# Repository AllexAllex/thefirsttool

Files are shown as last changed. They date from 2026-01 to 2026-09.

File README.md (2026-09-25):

# Информация о станках The First Tool (thefirsttool, firsttool, tool the first)

## Оглавление:
1. [Доработки](#раздел_доработки)
2. [Настройка станка](#раздел_настройка)
3. [3D модели для печати](#раздел_модели)
4. [Информация](#раздел_информация)
5. [Ссылки](#раздел_ссылки)
6. [Прочие дела станочные](#прочее)
   
## 1. Доработки 
- [Первая доработка - замена винтов](modification/screw-m3/screw-m3.md)
- [Фрезерный стол из станочного профиля](/modification/milling-table/milling-table.md)
- [Доработка тисков](modification/vise/vise.md)
- [Перевод на трапецидальную винт-гайку Т5 кареток станка](modification/screw-t5/screw-t5.md)
- [Замена втулок М6 на резьбовые втулки М6-М8](https://youtu.be/2hZVbYo9hZk)
- [Вращающиеся лимбы](modification/limb/limb.md)
- [Распиливание разжимных клинов](modification/sawing-wedge/sawing-wedge.md)
- [Оклеивание направляющих стальной лентой](modification/steel-tape/steel-tape.md)
- [Латунный клин в каретку](modification/brass-wedge/brass-wedge.md)
- [Выравнивание поверхности ласточкиного хвоста малой каретки](modification/low-feed-grinding/low-feed-grinding.md)
- [Исправление геометрии малой (поперечной) каретки](modification/small-feed-geometry/small-feed-geometry.md)
- [Прижимные винты клина подачи](modification/pressure-feed-screws/pressure-feed-screws.md)
- [Защита от стружки на шпиндель](modification/chip-protection/chip-protection.md)
- [Крепление фрезерной колонны (из двух длинных балок)](modification/milling-machine-column/milling-machine-column.md)
- [Крепление фрезерной колонны (из двух длинных балок) версия 2](modification/milling-machine-column-2/milling-machine-column-2.md)
- [Цанговый патрон ER20 на стандартный шпиндель](modification/er20/er20.md)
- [Проставка 25мм под моторный блок](modification/spacer-for-spindle/spacer-for-spindle.md)
- [Внедрение стального патрона и шпинделя с резьбой М14х1](modification/steel-lathe-chuck/steel-lathe-chuck.md)

## 2. Настройка станка 
- [Варианты сборки станков](/settings/assembly.md)
- [Регулировка плавности хода подачи](/settings/feed-flow.md)
- [Сборка и настройка фрезерного варианта станка](/settings/milling-machine.md)
- [Затяжка распорных клиньев](/settings/tightening-wedges.md)
  
## 3. 3D модели для печати 
- [Крышка моторного блока](/3d/engine-block-cover/engine-block-cover.md)
- [Защитный кожух на голову моторного блока для горизонтального фрезера](/3d/motor-protection-horizontal-milling/motor-protection-horizontal-milling.md)
- [Держатель ручки сверлильного станка](/3d/drilling-machine-lever-holder/drilling-machine-lever-holder.md)
- [Кондуктор для фрезеровки гаек Т5](3d/conductor-nuts-t5/conductor-nuts-t5.md)

## 4. Информация 
- [Ответы на часто задаваемые вопросы](/info/faq.md)
- [Сравнение станков The first tool с аналогами (Xendoll и тд)](/info/compare.md)
- [Чертежи частей станка](/info/drawings.md)
- [Каталог со всеми вариантами станков](/info/catalog.md)
- [Каталог частей станков](/info/catalog-parts.md)
- [Документы к станку: гарантийный талон, инструкция, сертификат](/info/passport.md)

## 5. Ссылки 
- [Наш канал в telegram](https://t.me/MiniLatheRussia)
- [Чат в telegram по модульным станкам The fist tools \ Xendoll \ Unimat и другим](https://t.me/TheFirstToolRussia)
- [Канал Игорь KLIV, много полезных доработок и примеров работ на станке](https://www.youtube.com/channel/UCZDuRbTqA5QuboGSG2y2jEQ)
- [Канал Эрик Плотник, много полезных доработок и примеров работ на станке](https://www.youtube.com/user/1149G)
- [Тема по станку на форуме судомоделистов](https://www.shipmodeling.ru/phpbb/viewtopic.php?t=72530)
- [Тема по станку на форуме Чипмейкер](https://www.chipmaker.ru/topic/144908/)

## 6. Прочие дела станочные

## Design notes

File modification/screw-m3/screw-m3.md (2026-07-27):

# Первая доработка - замена винтов

Первая и самая простая доработка на этом станке - заменить все винты с крестообразным шлицем, которые идут со станком на винты с внутренним шестигранником, так же подложить шайбу. Материал клиньев на основе цинка, достаточно мягкий, продавливается шляпкой болта достаточно просто. Вот на фото пример что бывает без шайбы. 

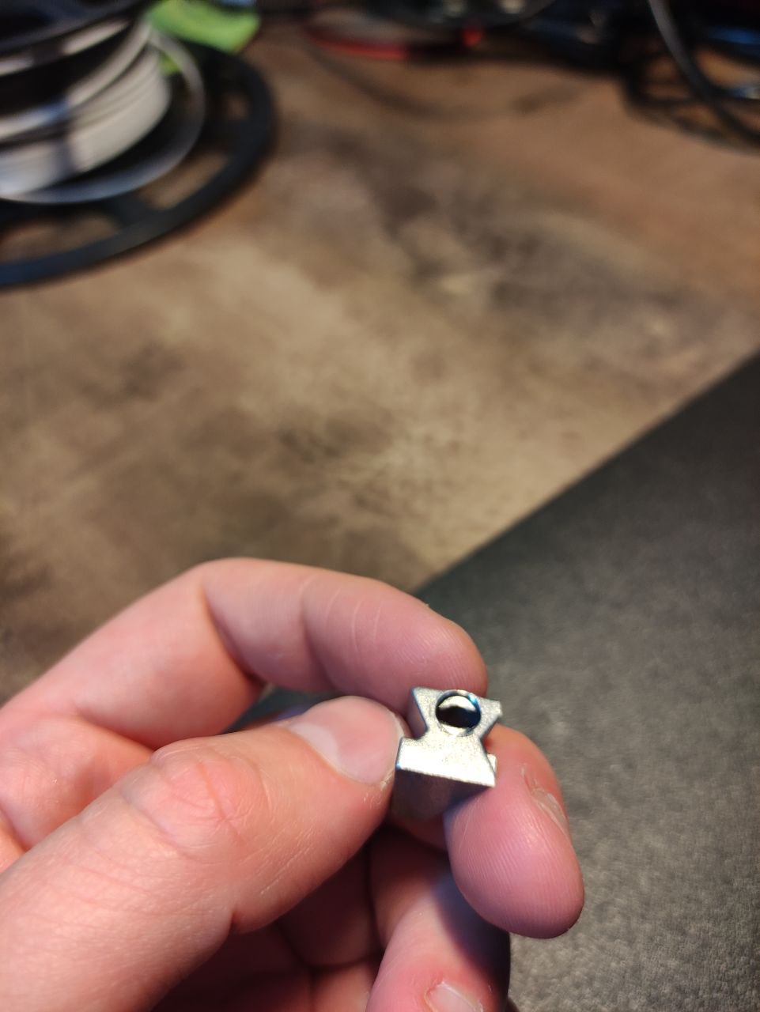
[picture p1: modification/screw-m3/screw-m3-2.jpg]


Ну и второе фото - с замененным винтом. Для коротких клинов м3х50, для длинных м3х70 (для распиленных), если не пиленые то м3х50

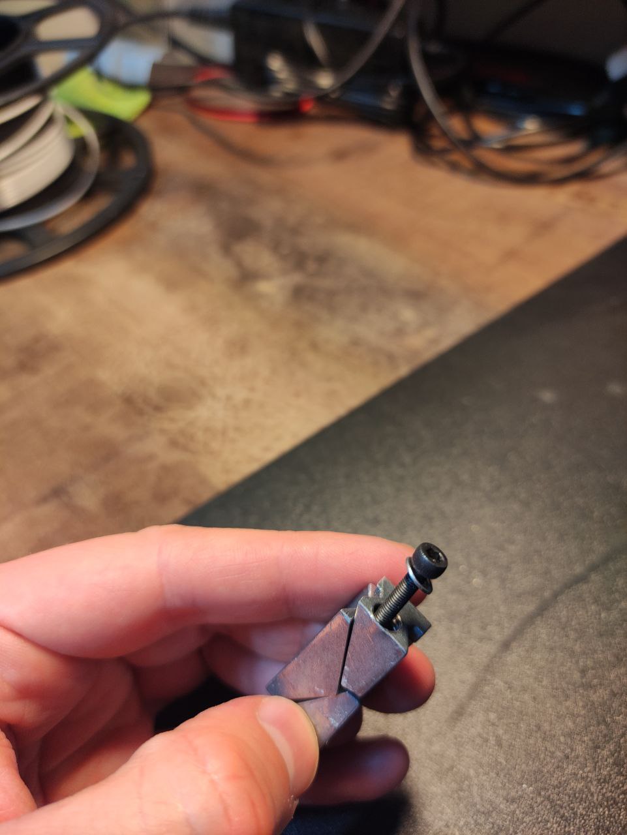
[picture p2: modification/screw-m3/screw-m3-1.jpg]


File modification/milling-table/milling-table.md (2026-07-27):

# Фрезерный стол

На станке не хватает большого фрезерного стола для работы с прижимами, в интернете продается заготовка профиль с т-пазами 200х110, я купил ее.
Для начала разметил центр стола и с помощью малой каретки наметил как она должна стоять и где примерно сверлить отверстия.

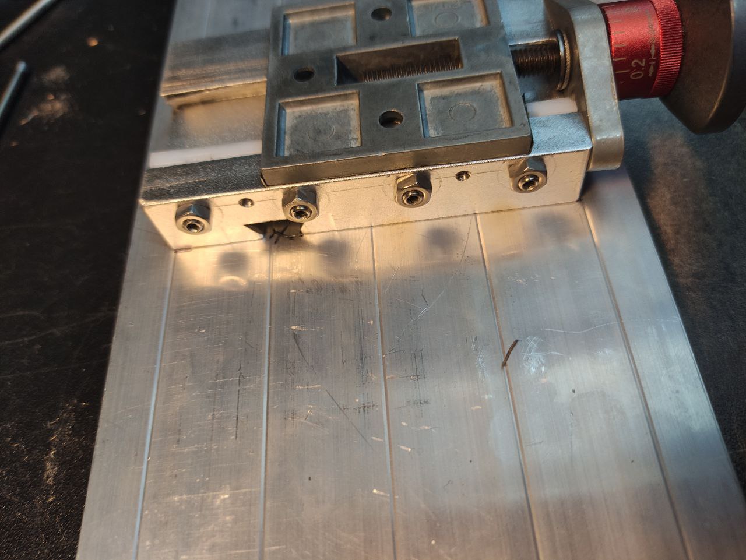
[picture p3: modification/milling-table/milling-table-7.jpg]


Далее с помощью тисков используя их как шаблон разметил отверстия.

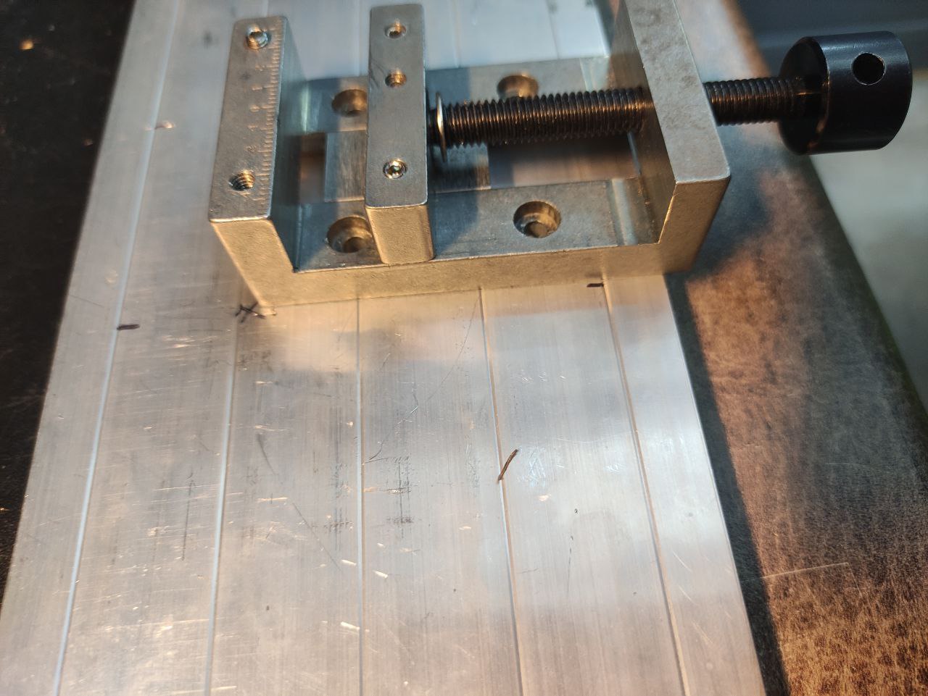
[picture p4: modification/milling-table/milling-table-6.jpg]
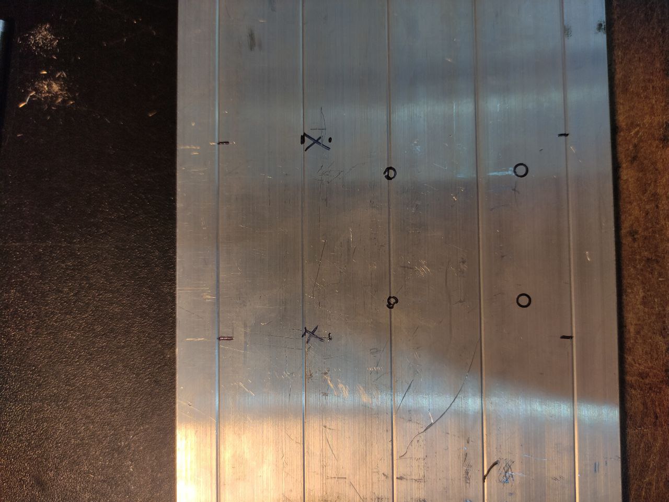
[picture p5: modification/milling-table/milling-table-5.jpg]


Есть у меня такой кондуктор для сверления отверстий, использовал его что бы проверлить первые два отверстия (сразу скажу что идея неудачная - кондуктор для столярных работ поэтому люфты в нем бешенные и точности в нем никакой нет, не используйте если у вас есть такой же). Правильное решение было бы - использовать угольник с широким основанием типа УШ-160 для разметки, либо штангенрейсмас если он у вас есть. 

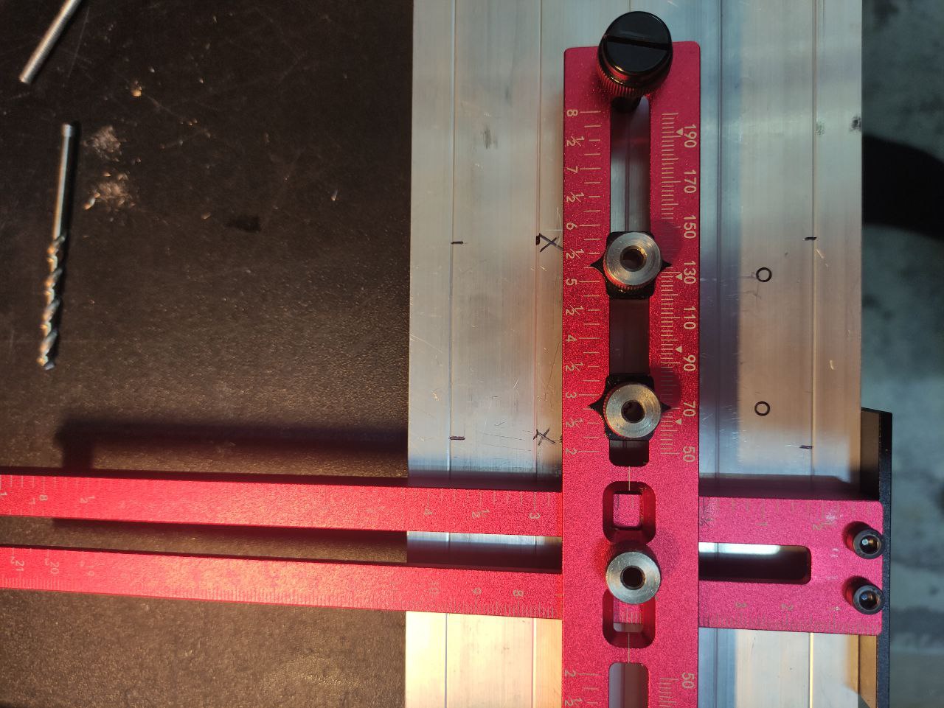
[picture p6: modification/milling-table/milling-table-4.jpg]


А дальше прикрутил тиски в эти два отверстия и сверлил уже через них используя их отверстия как кондуктор.

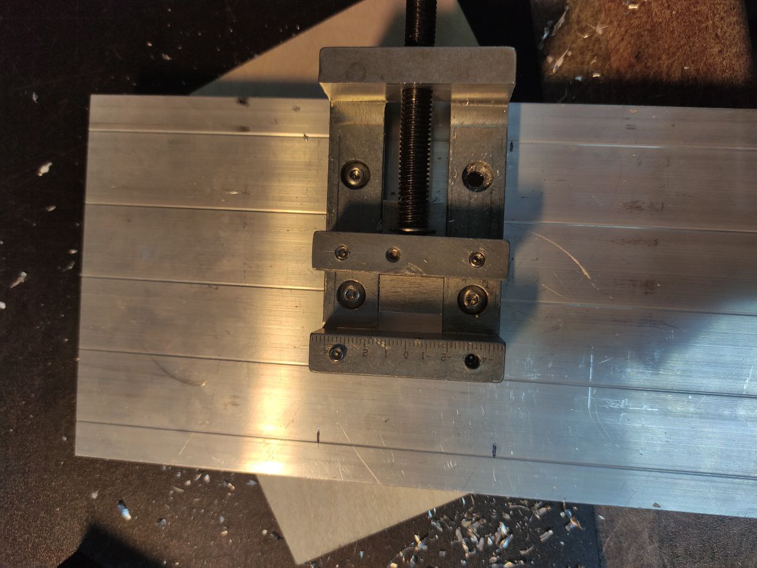
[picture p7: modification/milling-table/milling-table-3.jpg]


Дальше закрепил стол на поперечной каретке и отфрезеровал отверстия под шляпку болта фрезой 7мм которые совпали с ребром стола. Ну и готовый результат на фото.

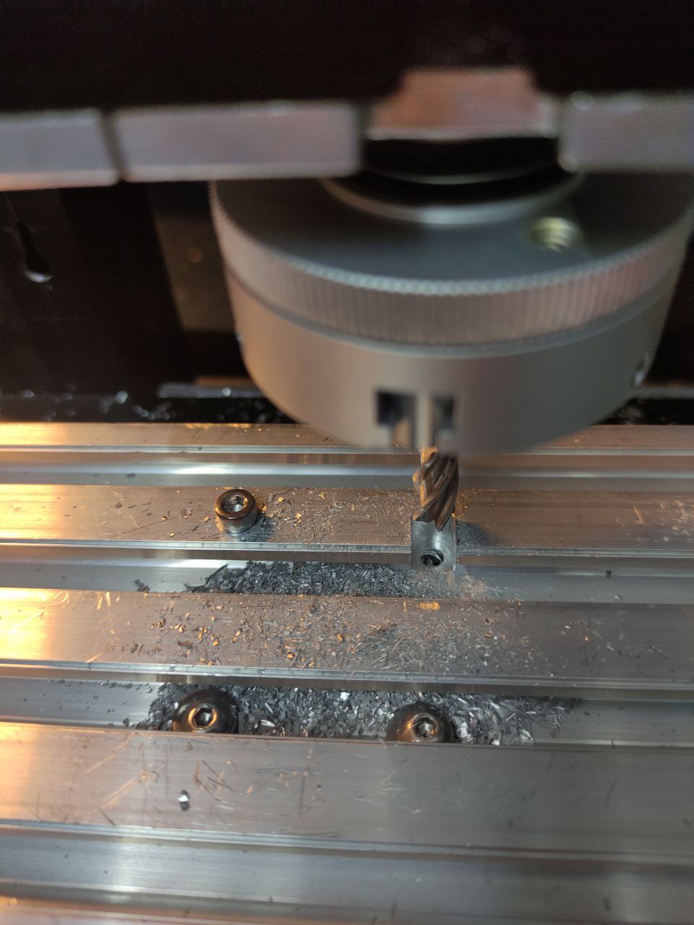
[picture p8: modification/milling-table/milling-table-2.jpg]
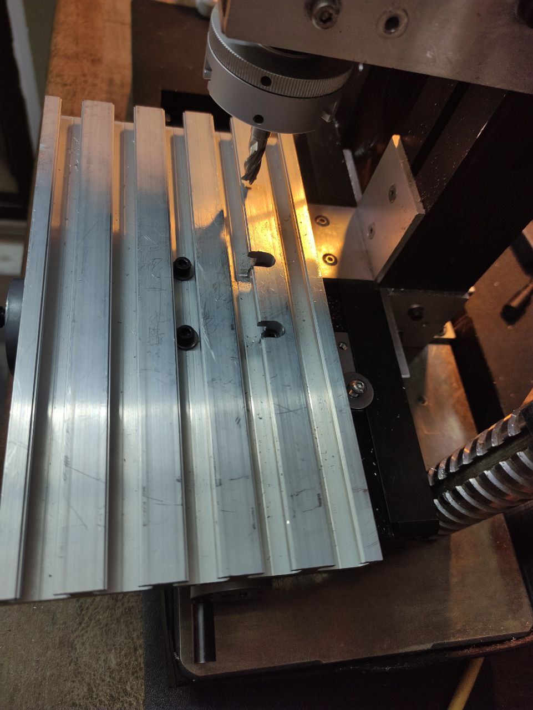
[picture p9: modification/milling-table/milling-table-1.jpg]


UDP: за кадром были сделаны еще 2 отверстия ниже, это позволило закреплять стол на 6 точках крепления, 4х оказалось мало и не всегда удобно. Так же используйте винты в "потай" либо с плоской шляпкой (они порядка 1.2мм в толщине) иначе из за головок болтов не удается закрепить прижим в нужных местах. Хотя сама по себе идея с таким большим столом получилась очень даже здравая для тех кто фрезерует довольно крупные для станочка заготовки. Я например распиливаю на горизонтальном фрезере заготовки длиной до 20см и толщиной до 15мм, их разумеется невозможно закрепить на стандартном столе каретки поперечной подачи.

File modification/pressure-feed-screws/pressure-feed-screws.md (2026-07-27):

# Прижимные винты клина подачи

Существует несколько проблем в системе прижима клина в каретках:
* Перекос клина. Штатные винты с острыми носиками к сожалению не давят строго по центру, они сильно смещены к верху, поэтому клин не прижимается равномерно к поскости ласточкиного хвоста. Это буду решать размещением новых винтов с точкой прижатия к клину ниже чем существющие винты
* Малое количество точек прижима. Для продольной подачи всего 3 точки прижима клина, для поперечной - 4. При такой системе прижима винта клин выгибает волнами в местах где проиходит давление винта, особенно это заметно на пластковом штатном клине. Во первых происходит быстрый износ клина в этих местах, во вторых при движении каретки при выходе из зацепления с ласточкиным хвостом такого места "выгиба" происходит небольшой сдвиг каретки, что отражается на точности. Добавлю точек прижима
* Острый носик у стола каретки, которым она упирается в ответную часть ласточкиного хвоста, а остальные поверхности остаются не прижатыми до конца. Уберу эти острые части которые не участвуют в прижиме.

Показал доработку на продольной каретке, добавлю дополнительные винты прижима, причем располагая их ниже чем штатные, в шахматном порядке. Для продольной подачи требуется добавить 2 новых винта прижима, для поперечной 3 винта.

В каретке просверлил отверстия 2.5мм между штатными винтами прижима и нарезал резьбу м3. Расстояние от низа каретки выбирал минимально возможное 3мм. Если сделать расстояние до поверхности меньше - будет вспучивать алюминий при нарезке резьбы. Винт прижима получился составной, сначала идет винт который прижимает сам клин, сверху его короткий установочный винт который вкручивается в это же отверстие и фиксирует от раскручивания первый.

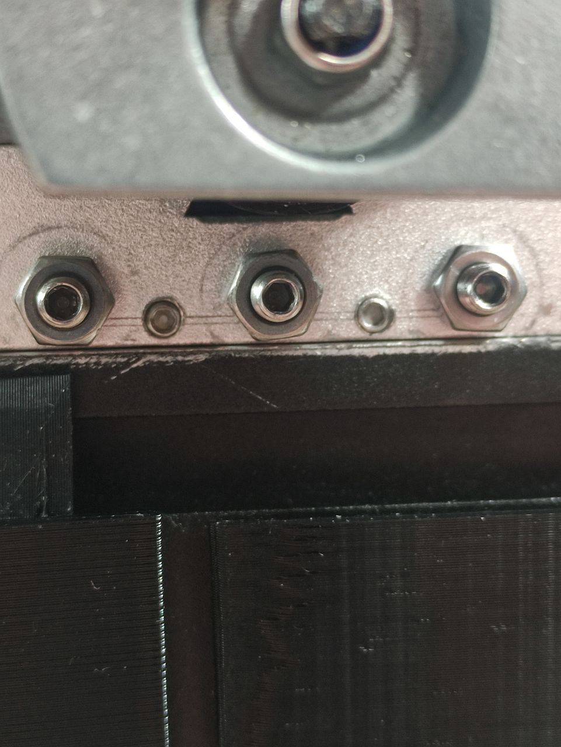
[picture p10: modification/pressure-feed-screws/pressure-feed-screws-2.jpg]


Так же убрал острые углы как на клине так и на каретке с прижимающихся к ластохвосту поверхностей. 
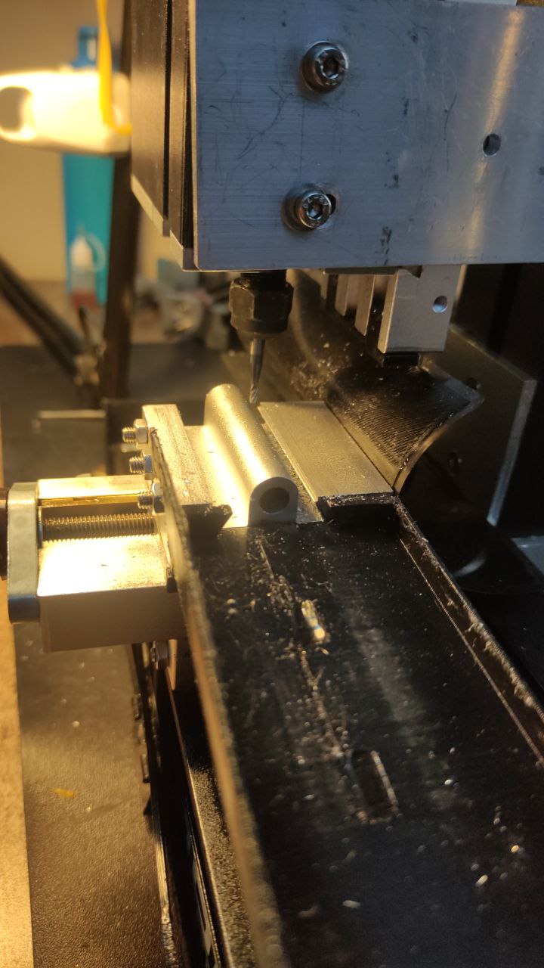
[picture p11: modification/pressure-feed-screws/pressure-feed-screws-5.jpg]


По итогу стал равномерный прижим как клина так и каретки к поверхностям направляющих. Ход каретки стал более плавным, а усилие прижима клина удалось увеличить

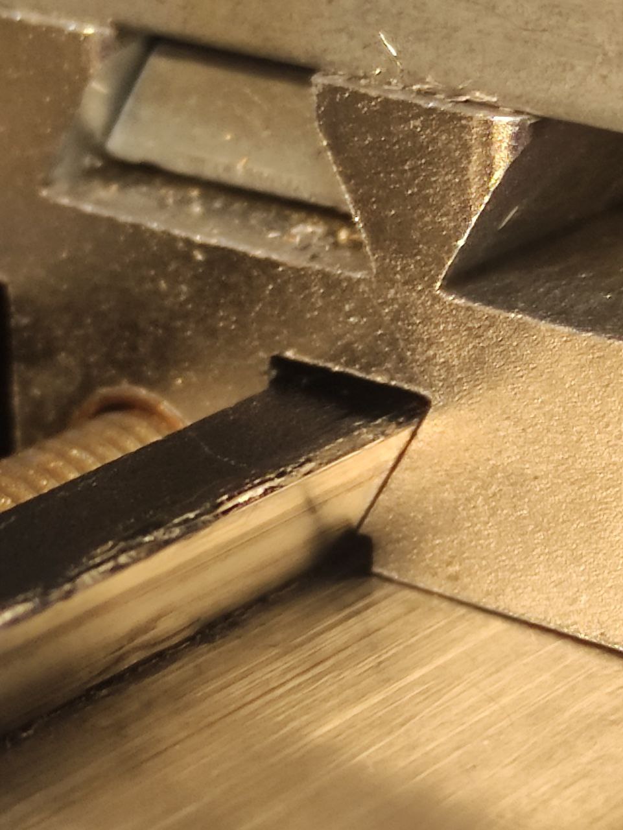
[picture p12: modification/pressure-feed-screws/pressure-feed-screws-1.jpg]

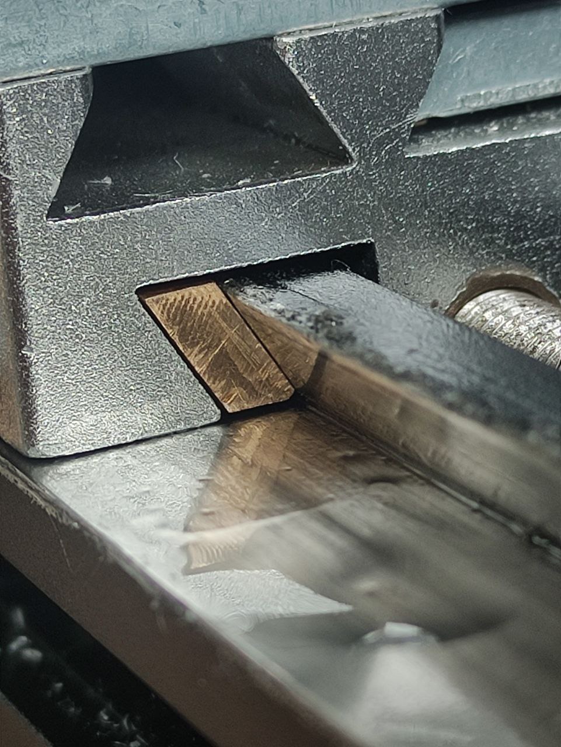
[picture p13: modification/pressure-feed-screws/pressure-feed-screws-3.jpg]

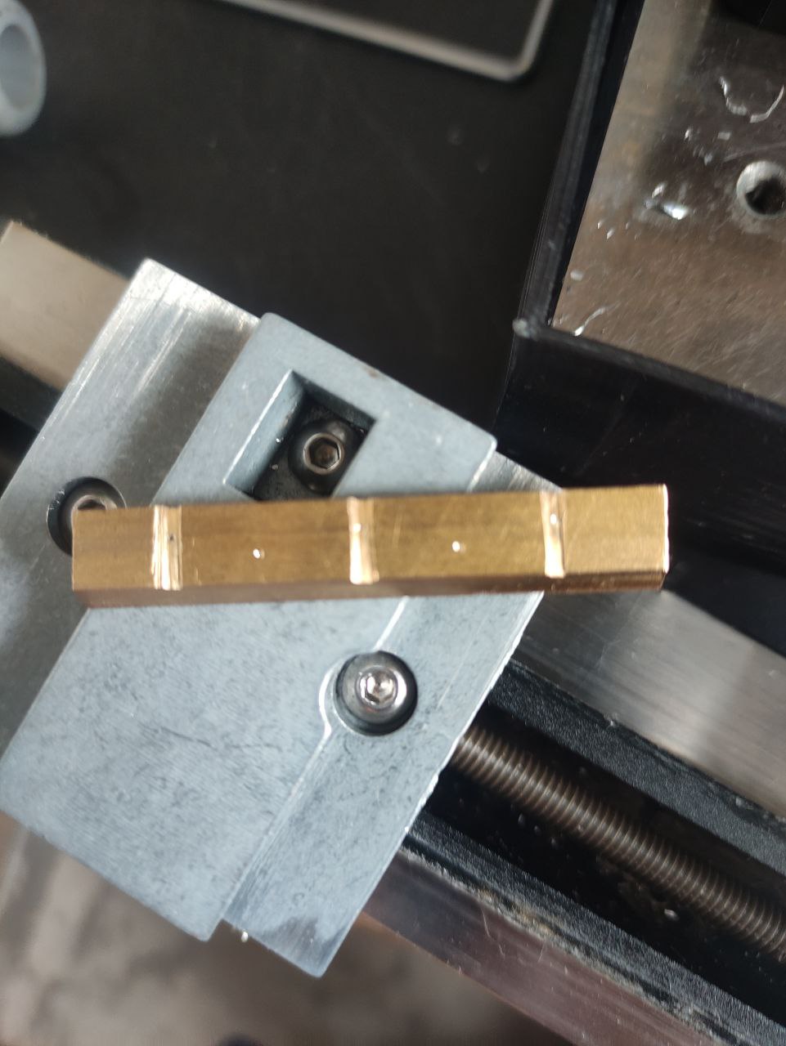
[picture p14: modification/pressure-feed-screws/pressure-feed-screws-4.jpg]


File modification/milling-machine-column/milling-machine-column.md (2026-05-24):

# Крепление фрезерной колонны 28см (устарела)

### [БОЛЕЕ ПРАВИЛЬНАЯ НОВАЯ ВЕРСИЯ ТУТ](https://github.com/AllexAllex/thefirsttool/blob/main/modification/milling-machine-column-2/milling-machine-column-2.md)

Купил себе вторую длинную балку 28см для того что бы сделать удлиненную станину фрезера, дело в том что сборка/разборка и выставление перпендикуляра между колонной и основанием долгое занятие, чтобы не мучаться решил что основание должно быть длинное. Так же это увеличит вес станка, что то же отлично. Для начала решил определиться а где у балки ровные углы 90град и ровные плоскости (на фото 1, 2 видно какое отличие в просвете), оказался всего 1 такой угол. 

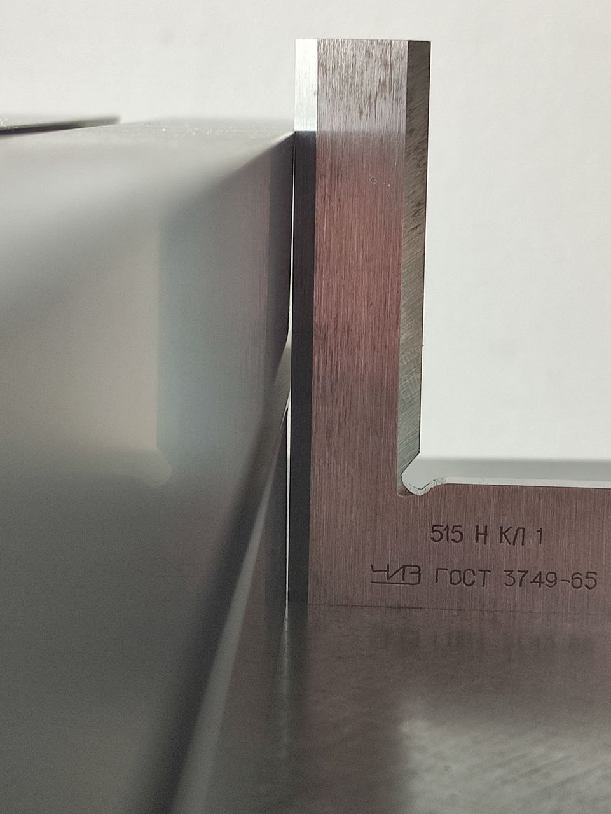
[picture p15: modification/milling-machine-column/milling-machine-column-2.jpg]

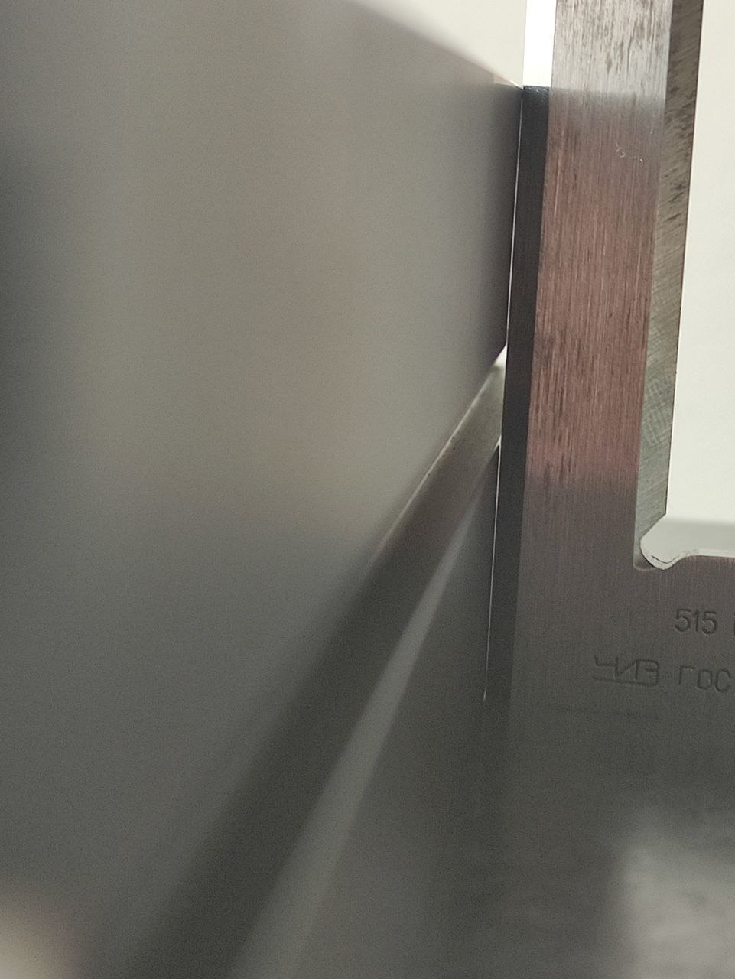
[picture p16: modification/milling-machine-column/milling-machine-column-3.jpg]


Использовал поверочную плиту и угольник. Пометил нужные мне плоскости и хороший угол. 

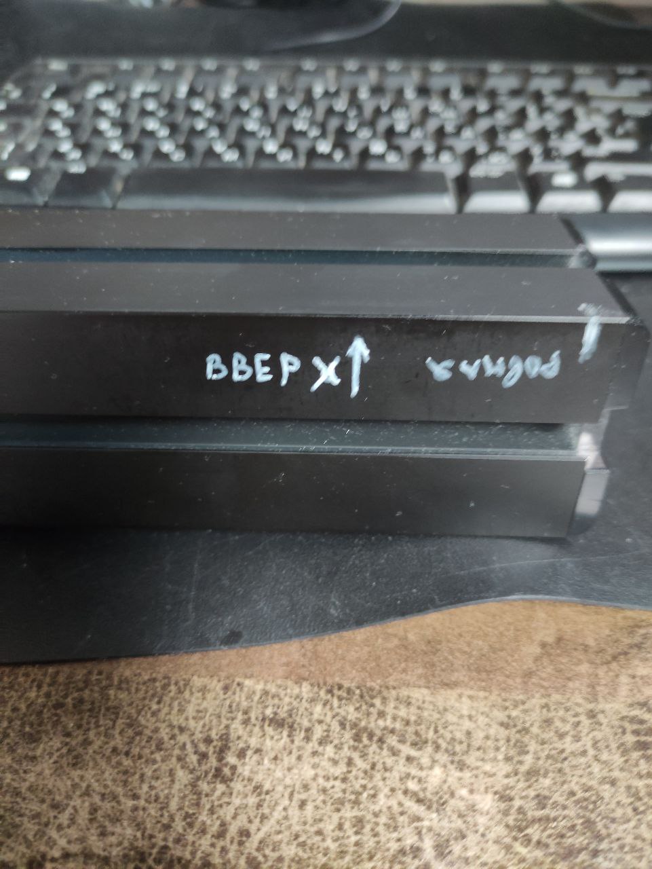
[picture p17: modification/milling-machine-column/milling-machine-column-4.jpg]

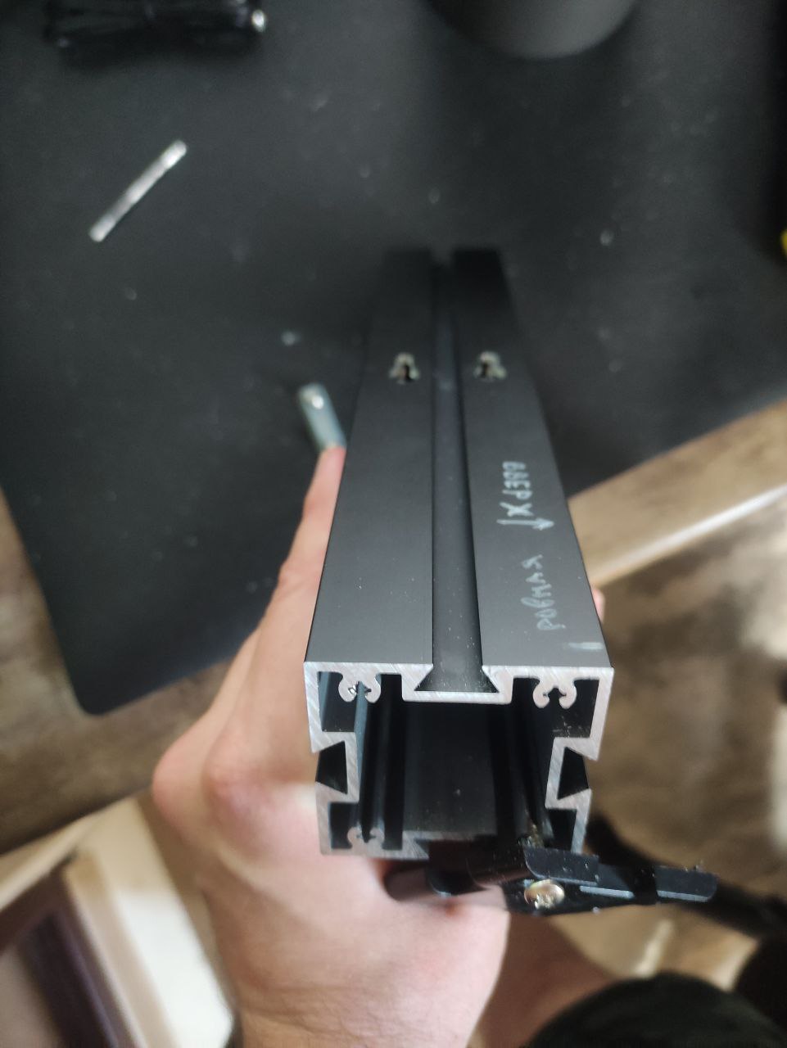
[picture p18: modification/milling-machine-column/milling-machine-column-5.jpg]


На ровной плоскости будем фрезеровать отверстие под крепления колонны. Увы они приходятся на область где проходит внутри крепления крышки, но ничего не поделать. С горем пополам отфрезеровал отверстия, а потом внутренюю область расширил т-образной фрезой под шляпки винтов.

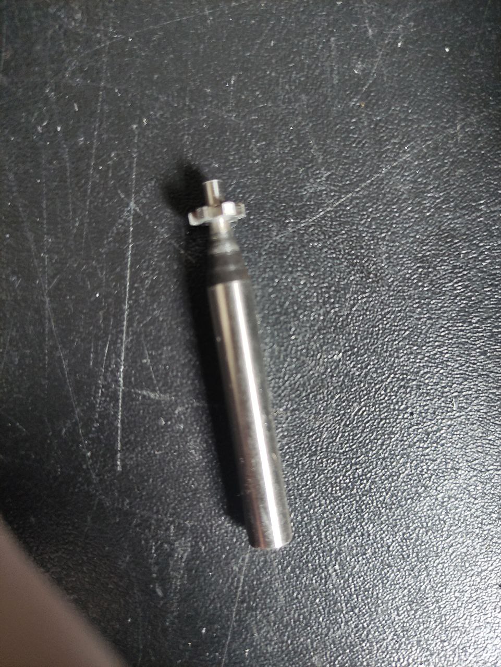
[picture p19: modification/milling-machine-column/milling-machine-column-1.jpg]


На фото финальный результат, за счет того что измерял лучший угол и плоскости удалось добиться хорошего угла между колонной и станиной без подкладок. Добавил еще один уголок крепления

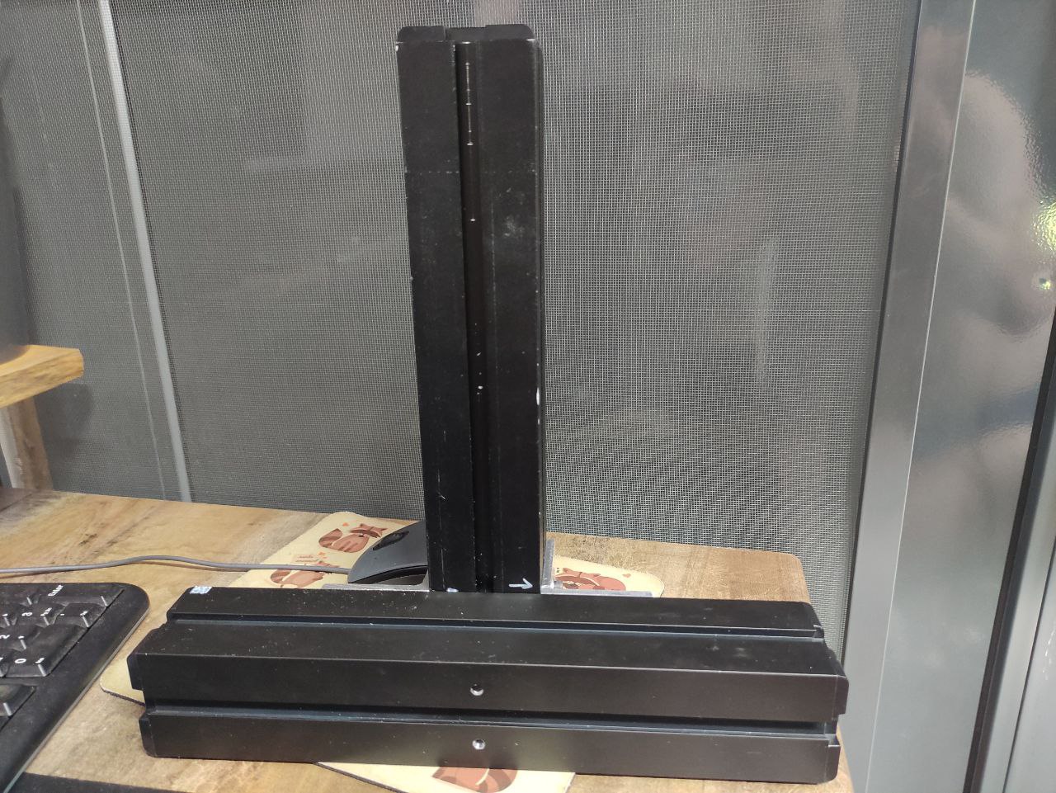
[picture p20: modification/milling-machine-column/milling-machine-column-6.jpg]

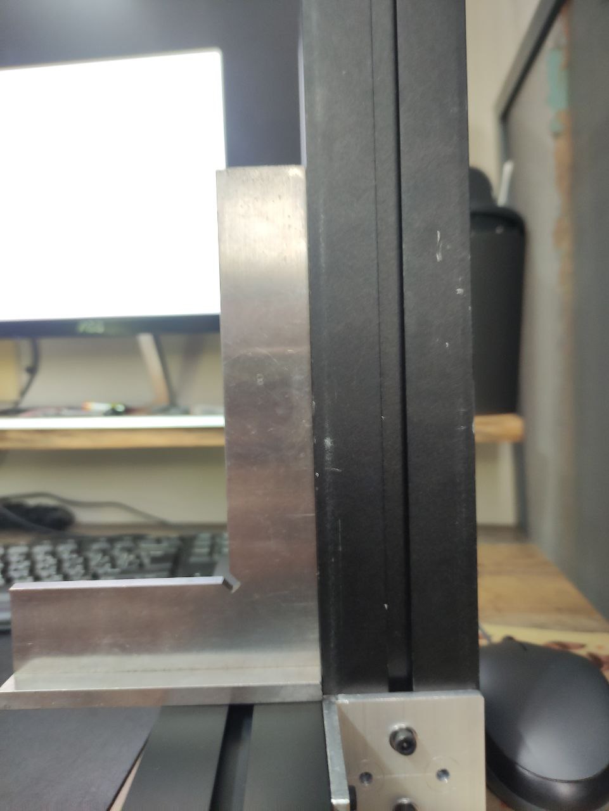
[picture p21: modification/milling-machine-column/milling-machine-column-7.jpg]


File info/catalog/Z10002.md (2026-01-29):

## Z10002 Сверлильный станок с поворотной осью и делительным устройством (УДГ)

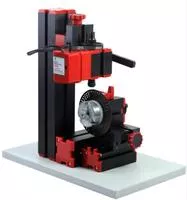
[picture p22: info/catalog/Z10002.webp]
Z10002


Drilling Machine With Dividing Plate Z10002

 Feature:
1. By using dividing plate, we can drill the round workpiece equally.
 2. There are three circles of the holes on the dividing plate and the number of the holes respectively is 36,40,48. We can choose them as needed.
3.Machine color is made up of red and black.
Technical parameters:
1.Motor speed :20,000rpm/min, motor blade and gear are made of metal.  
2.Input voltage/current/power:12VDC/2A/24W
3.Working material: wood, engineer plastic, soft metal(aluminum ,copper etc.)
4. Maximum workpiece diameter clamped by three-jaw chuck:50mm
5.The transformer has over-current protection, over-voltage protection, over heating protection

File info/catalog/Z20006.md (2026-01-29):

## Z20006 Шлифовальный станок

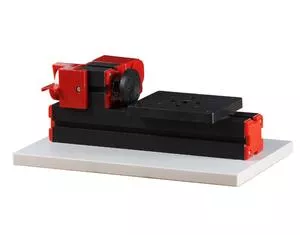
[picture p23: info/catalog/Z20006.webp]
Z20006


Sanding Machine Z20006

 Feature:
1.The left side of the machine has a small grinding wheel with a wheel guard.  
2.The machine can be used to polish , grin. If needed, we use the machine by hand to grind under any angle.  
3. Center height 25mm, sanding paper:100# ( optional) choose different sanding paper according different work pieces and workpieces surface. Machine color is made up of red and black. Technical parameters:
1.Motor speed :20,000rpm/min ,motor and gear are made of metal. 2.Input voltage/current/power:12VDC/2A/24W
 3
.Working table size：123 * 100mm
4.Working material: wood, engineer plastic, soft metal(aluminum ,copper etc.)
5.The transformer has over-current protection, over-voltage protection, over heating protection.

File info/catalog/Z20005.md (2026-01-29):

## Z20005 Фрезерный станок

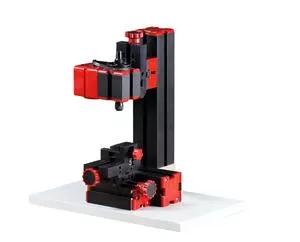
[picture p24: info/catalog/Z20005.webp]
Z20005


Milling Machine Z20005

 Feature:
1.The machine can be operated in X,Y,Z three dimensional space, can be assembled into vertical milling machine, horizontal milling machine and hand-held milling machine.  
2. Milling cutter, with two edges, is dangerous, so people should be guided by teachers when using it. 3.Machine color is made up of red and black.
Technical parameters:
1.Motor speed :20,000rpm/min ,motor and gear are made of metal. 2.Input voltage/current/power:12VDC/2A/24W
3.Slider travel:30mm，50mm
4.Collets：1-6mm
5、Working material size clamped by machine vice:30mm  6.Working material: wood, engineering plastic, soft metal(aluminum, copper etc.)
7. The transformer has over-current protection, over-voltage protection, over heating protection

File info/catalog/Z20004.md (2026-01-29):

## Z20004 Сверлильный станок

Z20004

Drilling Machine Z20004

 Feature:
1.Working material: wood board, plywood, soft meta(aluminum ,copper etc.),engineering plastic. Machine color is made up of red and black. Easy operation, it can be used to drill and grind by hand, and it can drill holes with equal ratio on the workpiece within 180 degrees by using dividing plate.
Technical parameter:
1.Motor speed :20,000rpm/min, motor and gear are made of metal
2.Input voltage/current/power:12VDC/2A/24W
3.Slider travel:30mm，50mm
4.Collets：1-6mm。 5.Working table size：123*100mm. 6.The transformer has over-current protection, over-voltage protection, over heating protection.

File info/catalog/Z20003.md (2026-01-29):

## Z20003 Токарный станок по дереву для обработки с помощью ручных резцов и упором

Z20003

Wood-turning Lathe Z20003

Feature:
  1.Softwood,  hardwood can be processed.
  2. Workpieces can be clamped by three-jaw chuck or collets(1-6mm),center height-25mm, distance between center- 135mm.
  Technical  parameters:
  1.Motor speed :20,000rpm/min, motor and gear are made of metal 
  4.Working  material length:135mm   
  2.Input voltage/current/power:12VDC/2A/24W 
  3.Maximum  working material diameter: 45mm
  6. The transformer has over-current protection, over-voltage protection, over heating protection.
  5.Working material: wood, engineering plastic, soft metal(copper, aluminum  etc.)

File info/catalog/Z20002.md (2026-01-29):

## Z20002 Токарный станок с подачами

Z20002

Metal Lathe Z20002

Feature:
  1.Working material: wood, and engineering plastic ，soft metal etc.  Machine color is made up of red and black. Motor blade and gear are made of metal.
  Technical parameters:    
  3.Maximum working   material diameter:20mm
  1.  Motor speed :20,000rpm/min
  2.Input voltage/current/power:12VDC/2A/24W
  5. The transformer has over-current protection, over-voltage protection, over heating protection.   Certificate Transformer passed: CE,UL
  4.Working material   length:135mm

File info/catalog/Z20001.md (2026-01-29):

## Z20001 Маятниковый лобзик

Z20001

Jigsaw Z20001

Feature：
  1.With special design, the reciprocating blade is touch safe in case of finger contact -it just causes slight vibration without cuts when  skin contacts. Motor blade and gear are made of metal.
  3. Machine color is made up of red and black.
  2. Allow straight-line cutting and curve cutting.
  2.Input voltage/current/power:12VDC/2A/24W 
  Technical parameters:    
  1.Motor speed :20,000rpm/min
  plywood-7mm, soft wood-18mm, aluminium-0.5mm, acrylic-2mm.
  3.Working table size:90mm*90mm    
  4.Maximum working material thickness: solid wood-4mm,
  protection, over heating protection.certificate Transformer
  5.The transformer has over-current protection, over-voltage
passed :CE,UL

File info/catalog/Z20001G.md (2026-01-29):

## Z20001G Лобзик с дуговым креплением пилки

Z20001G

Mini Bow-Arm Jigsaw Z20001G

Feature:
  1.With special design, the reciprocating blade is touch safe in  case of finger contact -it just causes slight vibration without cuts when   skin contacts. Motor blade and gear are made of metal. 
  2. Allow straight-line cutting and curve cutting.
  3. Machine color is made up of red and black.
  Technical parameters:
  4. Maximum working material thickness: solid wood-4mm,
  1.Motor speed :20,000rpm/min
  2.Input voltage/current/power:12VDC/2A/24W 
  3.Working table size:90mm*90mm        
  protection, over heating protection.
  plywood-7mm, soft wood-18mm, aluminium-0.5mm, acrylic-2mm.
  5.The transformer has over-current protection, over-voltage
  6. Withbow-shaped arm. The material of bow-shaped arm with its accessories is metal which increases its durability. Certificate transformer passed: CE,UL

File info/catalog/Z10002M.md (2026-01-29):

## Z10002M Сверлильный станок с поворотной осью и делительным устройством (УДГ)

Z10002M

Metal Drilling Machine With Dividing Plate Z10002M

 Feature:
1.Main parts: headstock, radial arm, long machine bed, short machine bed, small slider, big slider, motor blade, connection piece, dividing positioned, gear etc. All of the parts are made of metal.
2. By using dividing plate, we can drill the round workpiece equally.
3. There are three circles of the holes on the dividing plate and the number of the holes respectively is 36,40,48. We can choose them as needed.
Technical parameters:   
1.Motor speed :20,000rpm/min(optional choice 12,000rpm/min)
2. Input voltage/current/power:12VDC/2A/24W
3. Working material: wood, engineering plastic, soft metal (gold, silver, copper, aluminum etc.)
4. Maximum workpiece diameter clamped by three-jaw chuck:50mm
5. The transformer has over-current protection , over-voltage protection, over-heating protection .
6. With 0.02mm scale line, the hand wheel increases the precision when processing

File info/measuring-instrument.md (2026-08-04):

# Измерительный инструмент

Помимо станка, оснастки для него, заготовок и режущего инструмента, обязательно появится набор измерительного инструмента. Ниже я разделил такой измеритель на 3 категории, начиная с базовых вещей, заканчивая продвинутыми вариантами которые могут никогда не понадобится. Все ниже описано исходя из металлообработки на мини-станке типа The First tool \ Xendoll и аналогичных. Для деревообработки потребуется другой инструмент. Все что написано личное мнение автора исходя из скромного опыта, не претендующее на истину.

### 1. Это база.
Король измерений в обработке это конечно штангенциркуль и наверное он должен появится первым. Это универсальный инструмент измерения линейных размеров между точками на наружных и внутренних граней деталей, так же есть возможность замерять глубину отверстий\уступов с помощью щупа глубиномера. Их бывает много видов, но принципиально они либо нониусные (обычно с точностью 0.1мм или 0.05мм) либо цифровые (обычно с точностью до 0.01мм). Для новичка я советую выбрать цифровой, он проще в плане использования и точнее. На момент написания наверное лучше предпочесть какой нибудь качественный китай по соотношению цена\качество. Это SHAN, SHAHE, Insize. У меня клон митутоя, но я знал как его проверить и знал что его можно будет вернуть если мне не понравятся результаты проверок.

Угольник. Он нужен для разметки заготовок, выставления чего либо перпендикулярно, можно использовать его длинную сторону как поверочную линейку. Особенно он важен если будете использовать фрезерный вариант станка - тут без него никуда. Угольников бывает много видов, но я рекомендую первым из них приобрести типа УШ 160х100, с широким откручивающимся основанием. Довольно важно что бы угольник имел класс точности который обязательно должен быть нанесен на сам угольник, например (кл.1. кл.2, кл.3). Нам подойдет любой класс, но он должен быть. Угольники без класса точности - строительные, то есть угол между сторонами такого угольника может быть любой по сути, хоть и заявляют 90градусов на бумажке. Угольник из строительного магазина не подойдет в работе со станком, он предназначен только для строительства или деревообработки, где отклонения от угла 90градусов или криволинейность плоскостей ни на что не влияет. Как показала практика - угольники из Китая не соответствуют заявленным характеристикам, поэтому этот инструмент лучше поискать на интернет барахолках производства СССР, стоить по цене будет так же как и новый китайский.

### 2. Стандарт

Микрометр - он нужен что бы точно измерять линейные размеры, но только наружных поверхностей. Дело в том что штангенциркуль при всей своей универсальности имеет ряд недостатков и самые существенные из них это перекос рамки измерительной шкалы при некотором усилии прижима губок к детали, что нужно контролировать только руками и корректность измерения зависит только от ваших рук, поэтому обычно нужна серия измерений и усреднение показаний. Так же это перекос самого штангенциркуля относительно измеряемых поверхностей, он должен быть расположен строго под 90градусов, иначе можно получить завышенные измерения. Этих недостатков лишен микрометр - степень прижима губок контролируется трещоткой, а перекос микрометра относительно измеряемой поверхности легко устраняется за счет широкого основания измерительных губок. Микрометры бывают разных моделей и размеров, нам нужны нониусные с плоскими губками, хотя и цифровые хорошие, но дороже значительно. По размерам их очень большое количество, базовый микрометр 0-25, можно купить микрометры покрывающие диапазон измерений от 0 до 100мм, больше не нужно для мини станка.

Индикатор (часового типа) со стойкой. Он нужен для измерения размеров при перемещениях. Например можно померить биение заготовок в патроне, кривизну плоских поверхностей, параллельность каких то плоскостей. Он так применяется для выставления и проверки геометрии станка. Существуют как цифровые так и аналоговые, удобнее аналоговые (со стрелкой) ведь индикатор отслеживает именно изменение размера, а изменение удобнее по стрелке смотреть. Зато у цифрового есть сброс в ноль и возможность удобного относительного измерения, так же цифровые можно купить с большим пределом измерений 0-12мм и высокой точностью до микрона - 0.001мм. Удобно когда есть оба варианта и аналоговый типа ИЧ-10, так и цифровой на диапазон 0-12, но чаще я пользуюсь аналоговым (часового типа). Индикатор нужно крепить в стойку, поэтому нужно ее сразу купить. Из Китая продается маленькая красная стойка - то что нужно для мини станка, это хорошие стойки. 

Поверочная линейка нужна для измерения плоскостности деталей на просвет (для линеек со скосом типа ЛД, ЛТ, ТЧ), либо для работы со щупами для линеек типа ШД, ШП.

Щупы измерительные, радиусомеры, шаблоны для измерения резьб. Нужны что бы измерять существующие детали, например радиус закругления, резьбу в гайке или на шпильке\винте. Щупы нужны для измерения зазоров между поверхностями, например между поверочной линейкой и измеряемой поверхностью. Вещи которые часто в работе, стоят недорого.

Штангенрейсмас - служит для точной разметки деталей и для измерения относительно плоскости на которой он стоит подошвой. Для небольших деталей которые и будем обрабатывать на станке - идеален штангенрейсмас 0-200, но более распространенные 0-250, такой то же подойдет. А вот размером больше - брать не советую, слишком они неудобные для мелких деталей. Продают так же пластиковые штангенрейсмасы по привлекательной цене - не советую, в этом деле нужна жесткость - пластик ее обеспечить не сможет и никакой точной разметки не получится. Новый штангенрейсмас стоит довольно дорого, поэтому ищите на интернет-барахолках, там не столь высокие цены на них.

### 3. Полный комплект

Угломер нониусный или оптический

Набор КМД

Поверочная плита

Микрометр рычажный

Индикатор рычажного типа (ИРБ)

Нутромеры или штихмасс.

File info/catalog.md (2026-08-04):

## Каталог существующих вариантов станков The first tool. Информация с [официального китайского сайта](http://www.zhouyurobot.com/)
Перевод с авторскими пояснениями.

### Базовые пластиковые "красно-черные" модели.
Визульное оформление красно-черный пластик. Это модели сделанные в основном из пластика, имеющими самую низкую жесткость и малую мощность 24Вт. Подходят для обучения детей на обработке пластика и дерева. Из плюсов низкая цена и относительная безопасность. Дата начала производства 2008г.
- [Z20001G](catalog/Z20001G.md) Лобзик с дуговым креплением пилки
- [Z20001](catalog/Z20001.md) Маятниковый лобзик
- [Z20002](catalog/Z20002.md) Токарный станок с подачами
- [Z20003](catalog/Z20003.md) Токарный станок по дереву для обработки с помощью ручных резцов и упором
- [Z20004](catalog/Z20004.md) Сверлильный станок
- [Z20005](catalog/Z20005.md) Фрезерный станок
- [Z20006](catalog/Z20006.md) Шлифовальный станок
- [Z10002](catalog/Z10002.md) Сверлильный станок с поворотной осью и делительным устройством (УДГ)
  
### Металлические станки малой мощности
Визульно полностью черные с алюминиевыми деталями. Моторный блок из черного пластика, имеет характерноую скругленную с одного угла форму. Имеют металлические части как у более взрослых моделей, но моторный блок малой мощности 24Вт. 
В наименованиях моделей содержит букву M (Metal) после цифры. Подходит для обучения более старших детей, для работы в кружках. Дата начала производства 2010г.
- [Z20001MG](catalog/Z20001MG.md) Лобзик с дуговым креплением пилки
- [Z20001M](catalog/Z20001M.md) Маятниковый лобзик
- [Z20002M](catalog/Z20002M.md) Токарный станок с подачами
- [Z20003M](catalog/Z20003M.md) Токарный станок по дереву для обработки с помощью ручных резцов и упором
- [Z20004M](catalog/Z20004M.md) Сверлильный станок
- [Z20005M](catalog/Z20005M.md) Фрезерный станок
- [Z20006M](catalog/Z20006M.md) Шлифовальный станок
- [Z10002M](catalog/Z10002M.md) Сверлильный станок с поворотной осью и делительным устройством (УДГ)
  
### Основная линейка металлических станков с высокой мощностью.
Полностью из алюминиевых деталей анодированых либо крашенных черной краской с деталями из алюминия и цинкового сплава без анодировки. В наименованиях моделей содержит букву M (Metal) после цифры и букву T первой в имени модели. 
Моторный блок мощностью 60Вт. Предназначен для хобби и для работы с кружках. Может обрабатывать дерево, пластик, все цветные металлы. Дата начала производства 2012г.
- [TZ20001MG](catalog/TZ20001MG.md) Лобзик с дуговым креплением пилки
- [TZ20001M](catalog/TZ20001M.md) Маятниковый лобзик
- [TZ20002M](catalog/TZ20002M.md) Токарный станок с подачами
- [TZ20003M](catalog/TZ20003M.md) Токарный станок по дереву для обработки с помощью ручных резцов и упором
- [TZ20002MG](catalog/TZ20002MG.md) Токарный станок с подачами и увеличенным расстоянием от станины
- [TZ20002MR](catalog/TZ20002MR.md) Токарный станок с подачами и увеличенным расстоянием от станины с дополнительной малой продольной кареткой и поворотным модулем
- [TZ20003MB](catalog/TZ20003MB.md) Токарный станок по дереву для обработки с помощью ручных резцов и упором с увеличенным расстоянием от станины и длинной станиной 510мм. Межцентровое расстояние 300мм.
- [TZ20004M](catalog/TZ20004M.md) Сверлильный станок
- [TZ10002M](catalog/TZ10002M.md) Сверлильный станок с поворотной осью и делительным устройством (УДГ)
- [TZ20005M](catalog/TZ20005M.md) Фрезерный станок
- [TZ20005MA](catalog/TZ20005MA.md) Фрезерный станок с расточной фрезой, модификация "А"
- [TZ20005MF](catalog/TZ20005MF.md) Станок для изготовления "бусин"
- [TZ20006M](catalog/TZ20006M.md) Шлифовальный станок
- [TZ10001M](catalog/TZ10001M.md) Ручная шлифовальная\полировальная машинка
- [TZ20001MCZ](catalog/TZ20001MCZ.md) Торцевая пила
- [TZ10002MS](catalog/TZ10002MS.md) Шестиосевой фрезерно-сверлильный станок

### Металлические станки с LCD-экраном на каретках подачи, аналог УЦИ
Полностью повторяет основную серию металлических станков, но добавлен модуль с дисплеем отображающим перемещения по осям. Модуль обладает возможностью сбросить показания в ноль, показания как в метрической так и в дюймовой системе. 
Функция запоминания последнего показания, функция автоматического засыпания через минуту. Точность модуля 0.01мм, питание от батарейки 1.5В. 
Очень ограниченная серия, видммо так и не успевшая дойти до массового рынка, либо так и оставшаяся в Китае. В наименованиях моделей содержит букву D (Digital) в начале имени модели. Дата начала производства 2015г.
- [DTZ20004M](catalog/DTZ20004M.md) Сверлильный станок
- [DTZ20005M](catalog/DTZ20005M.md) Фрезерный станок
- [DTZ10002MZ](catalog/DTZ10002MZ.md) Фрезерный станок с расточной головкой с поворотной осью и делительным устройством (УДГ)
- [DTZ20002MG](catalog/DTZ20002MG.md) Токарный станок с подачами и увеличенным расстоянием от станины
- [DTZ20002MR](catalog/DTZ20002MR.md) Токарный станок с подачами и увеличенным расстоянием от станины с дополнительной малой продольной кареткой и поворотным модулем
- [DTZ20005MF](catalog/DTZ20005MF.md) Станок для изготовления "бусин"

### Металлические станки с числовым программным управлением (ЧПУ)
Это металлические станки в которых на оси перемещения добавлены шаговые двигатели и плата управления ими на основе mach3 или собственной Zhouyu industrial system. Максимальное количество осей с ЧПУ - 4. Заявленная точность обработки 0.07мм. Вторая буква в имени модели C (CNC). Видимо из за очень высокой цены данная серия не имела распространения. Дата начала производства 2012г.
- [TCZ10002MZ1](catalog/TCZ10002MZ1.md) 4х осевой сверлильно-фрезерный станок
- [TCZ20005MM](catalog/TCZ20005MM.md) горизонтальный фрезерный станок
- [TCZ20005MTF](catalog/TCZ20005MTF.md) 4х осевой фрезерный станок, модификация с задней бабкой
- [TCZ4000M](catalog/TCZ4000M.md) 3х осевой сверлильный станок
- [TCZ20005M](catalog/TCZ20005M.md) 3х осевой сверлильно-ферезерный станок
- [TCZ20002MG](catalog/TCZ20002MG.md) Токарный станок с подачами и увеличенным расстоянием от станины
- [CZ20002MT](catalog/CZ20002MT.md) Токарный станок с подачами и увеличенным расстоянием от станины с мотороным блоком с шаговым двигателем
- [TCZ10002M](catalog/TCZ10002M.md) 4х осевой сверлильно-фрезерный станок, без поворотного блока шпинделя
  
### Наборы станков.
Поставляются в 2х вариантах коробок. Пластиковый короб для варианта где есть станок лобзик с дуговым крепленим пилки. Картонная коробка - остальные варианты. Дата начала производства 2012г.
- [Z4000](catalog/Z4000.md) 4 базовых пластиковых станков
- [Z6000](catalog/Z6000.md) 6 базовых пластиковых станков
- [Z8000](catalog/Z8000.md) 8 базовых пластиковых станков
- [Z4000M](catalog/Z4000M.md) 4 металлических станков малой мощности 24Вт
- [Z6000M](catalog/Z6000M.md) 6 металлических станков малой мощности 24Вт
- [Z8000M](catalog/Z8000M.md) 8 металлических станков малой мощности 24Вт
- [TZ6000M](catalog/TZ6000M.md) 6 металлических станков большой мощности 60Вт
- [TZ8000M](catalog/TZ8000M.md) 8 металлических станков большой мощности 60Вт
- [TZ10000MZG](catalog/TZ10000MZG.md) 10 металлических станков большой мощности 60Вт
- [TZ20000MZG](/catalog/TZ20000MZG.md) 20 металлических станков большой мощности 60Вт

### Существуют другие комплектации станков которые продавцы придумали на свой вкус. Например известны следующие модели которых не было в официальном каталоге, но они существуют у продавцов
- [TZ20005MM](catalog/TZ20005MM.md)  Горизонтальный фрезерный станок, металлический, 60Вт
- [TZ20002MGL](catalog/TZ20002MGL.md) TZ20002MLB Токарный станок с подачами на длинной базе 510мм, металл, 60Вт
- [TZ10003MS](catalog/TZ10003MS.md) 6-осевой обрабатывющий станок с 2мя моторными блоками, металл, 60Вт

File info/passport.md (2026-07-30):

## Оригинальные документы от станка TZ20005M (металлический фрезерный станок, 60Вт)

Гарантийный талон





Сертификат



Инструкция по сборке и эксплуатации





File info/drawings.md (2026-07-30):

### Чертежи взяты с [форума судомоделистов, где их сделал пользователь Stasys](https://www.shipmodeling.ru/phpbb/viewtopic.php?t=72530&start=180)
Скопировано что бы избежать утраты чертежей

Пример соединения двух продольных кареток, чертежи ручки


Основные профили станка, разрезы кареток, корпус моторного блока


Альтернативные резцедержатели которые можно купить


Варианты альтернативных тисков и разметка под сверловку отверстий


Валы шпинделя


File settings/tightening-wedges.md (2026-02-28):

Задался вопросом, а как сильно затягивать соединительные клины? На первый взгляд до упора, чем больше прижатие к стенкам ластохвоста тем лучше. А вот и нет! Все дело в пустотелых балках. Чем больше усилие затяжки - тем больше деформация самих балок, выгибание поверхности горбом. А когда нет прилегания поверхностей появляется раскачивание сопрягаемой поверхности на этом горбе - прощай жесткость. Если не затягивать клины так же не пойдет - усилие на срыв будет недостаточно или прижатие плоскостей не произойдет с достаточным усилием. В общем тут нужен баланс затяжки. В видео показал как я регулирую затяжку клиньев
[Видео](https://t.me/MiniLatheRussia/232)

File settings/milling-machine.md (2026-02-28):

Сегодня хочу рассказать как настроить фрезерный вариант станка.
Самое главное здесь выставить углы 90 градусов между:
- передней поверхностью колонны и верхней поверхностью балки
- боковой поверхностью колонны и верхней поверхностью балки
- параллельность вертикальной каретки между боковой поверхностью колонны и боковой каретки
- перпендикуляр между боковой поверхностью поперечной каретки и передней поверхностью колонны
Остальные углы в станке не регулируются.
Для регулировки нам понадобятся
- угольник с широким основанием типа УШ160х100
- стойка индикаторная и индикатор
- чистые поверхности станка, без стружки, без забоин
И так приступаем. Начнем с угла между передней поверхностью колонны и верхней поверхностью балки.
- Здесь главный секрет выставления правильная последовательность затяжки винтов прижимающей планки, надо начинать с нижнего винта, зажав его с достаточной силой, но не пережав что бы не выгнуло саму балку. Контролируем угольником, колонна должна завалиться назад. После этого подтягиваем верхним винтом, выравнивая колонну к вертикаль и постоянно контролируем угольником, доводим до 90 градусов (отсутствие просвета между поверхностью колонны и угольником).
- Следующий угол выставляем между боковой поверхностью колонны и верхней поверхностью балки. Устанавливаем угольник между этими поверхностями и небольшими ударами лево-право по колонне добиваемся 90 градусов. Контролируем что предыдущий выставленный угол не ушел. Теперь нужно закрепить усиливающие уголки со всех сторон. Здесь важно сначала зажать все болты на колонне, а только потом болты закрепляющие на балке, иначе в результате затяжки только что выставленные углы уйдут.
Теперь можно установить вертикальную и продольную подачи.
- Выставляем параллельность хода каретки относительно боковой поверхности колонны. Сначала надо снять фланец ручки и ходовой вал каретки, иначе поворот ручки будет вносить большую погрешность в измерения. Прижим клина выставить таким образом что бы каретка перемещалась руками с небольшим усилием,  но не люфтила и не падала вниз. Крепим индикатор на каретку, а щуп индикатора должен ходить по боковой поверхности колонны. Крепление 2х винтов каретки должно бы в меру расслаблено, а центрального - затянуто, таким образом будем иметь возможность поворота каретки по вертикальной оси. Постукивая по краям каретки и перемещая каретку рукой контролируем отклонение от паралельности. У меня получилось отклонение порядка 0.02мм на весь ход вертикальной каретки.
- Выставляем перпендикуляр между боковой поверхностью поперечной каретки и передней поверхностью колонны. Это удобно делать с помощью угольника, его подошву разместив на колонне и контролируя зазор между угольником и боковой поверхностью каретки. Винты крепления так же должны быть в меру ослаблены и постукиванием можно поворачивать каретку в нужную сторону. Не забываем затягивать все винты крепления после настройки.
В принципе на этом настройку можно считать законченной и остался этап контроля.
Здесь можно промерить получившиеся углы между вертикальной и столом поперечной подачи с помощью угольника и индикатора в разных плоскостях. У меня получилось фактически отклонение 0.02мм на весь ход каретки. Думаю что от этого станка нет смысла требовать большей точности.
Себе для лимит максимальных отклонения ставил 0.04-0.05мм на ход каретки, что было достигнуто.

[Видео с настройкой](https://t.me/MiniLatheRussia/293)

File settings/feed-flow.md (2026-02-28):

Показываю как правильно регулировать затяжку поджимающих винтов клиньев подач. 
С одной стороны подачи не должны закусывать или ходить слишком туго, во первых сложно крутить, во вторых во время фрезерования будет отгиб подачи то вверх то вниз из за усилий вращения ручки. 
Так же будет сильно изнашиваться ходовая латунная гайка в подаче из за сильного трения в ней. 
С другой стороны нельзя делать слишком прослабленный ход подачи, сильно теряется жесткость, появляются вибрации при обработке и тд. 
С опытом многократной регулировки станка нашел оптимальный способ регулировки обеспечивающий плавность и мягкость хода подачи, с другой стороны позволяющий ее настроить без люфта. 
Отдельно стоит сказать что нужно обеспечить одинаковость настройки по всей длине хода подачи, а это может быть в частности из за кривого расположения фланца вала ручки подачи, 
поэтому чем ближе к ручке подачи находится стол подачи, тем жестче она идет. 
Нужно обязательно расслаблять и подстраивать фланец ручки подачи. 
Так же надо обеспечить одинаковость затяжки винтов, что невозможно без снятия винта.
В видео показываю как все это сделать легко и быстро
[видео по настройке](https://t.me/MiniLatheRussia/233)

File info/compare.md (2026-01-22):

## Сравнение станков The first tool, производитель Shenzhen Zhouyu Intelligent Technology Co., Ltd с аналогичными модульными станками.
Сравниваются металлические версии с самыми мощными двигателями доступные для покупки у производителя

| Параметр \ Производитель | The first tool (Zhouyu) | Xendoll | ZHRUI |  Unimat ML (The Cool Tool) |
|--|--|--|--|--|
| Тип крепления | Ласточкин хвост | Т-паз | усиленный Т-паз | Т-паз |
| Максимальная мощность | 60Вт | 36Вт | 36Вт | 36Вт |
| Материал основных частей | усиленный алюминий (например АМГ3), цинковый сплав | алюминий | алюминий | алюминий |
| Цветовое решение | Черный | Синий с хромом | Серебристый с черным | Черный |
| Разнообразие вариаций станка | очень много | много | очень мало | очень много |
| Разнообразие частей в продаже | очень много | много | мало (условно подходят от Xendoll) | нет, только комплекты (условно подходят от Xendoll)|
| Цена | средняя | низкая | высокая | очень высокая |
| Заявленная точность (цена деления лимба) | 0.04 | 0.1 | 0.02 | 0.05 |
| Шаг винта | 1мм за оборот | 2мм за оборот | - | 1мм за оборот |
| Пластиковые детали | крышки-заглушки балки, клин в каретках | - | - | крышки-заглушки балки, клин в каретках |
| Обрабатываемые материалы | пластик, дерево, цветные металлы | пластик, дерево, алюминий малым сьемом (мало мощности двигателя) | пластик, дерево, алюминий малым сьемом (мало мощности двигателя) | пластик, дерево, алюминий малым сьемом (мало мощности двигателя) |

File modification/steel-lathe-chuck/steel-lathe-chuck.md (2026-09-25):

# Внедрение шпинделя м14х1 под стальной токарный патрон

В штатном варианте станок поставляется с цинковым патроном (цинковый сплав), довольно сомнительного качества (как и все в штатном виде это литье без постобработки с соответствующим отсутствием геометрии). Заготовки он зажимает плохо, стальные заготовки обрабатывать в нем практически не получится. Кулачки быстро изнашиваются. Единственное его преимущество это наличие ответного конуса для штатного шпинделя и наличие резьбы м12х1 соответствующей резьбе штатного шпинделя. Существуют алюминиевые патроны с резьбой М12х1 намного лучшего качества изготовления, здесь уже можно рассчитывать на неплохую геометрию, минимальные биения, и относительно неплохое зажатие (я даже обрабатывал сталь в таком патроне). Если вы не собираетесь менять штатный шпиндель - тогда советую такой вариант. На фото слева штатный патрон, справа - алюминиевый отдельно купленный, видно различие между ними (на кулачках у алюминиевого есть технологические отверстия, а с задней стороны патрон плоский).



Существуют и стальные патроны с резьбой м12х1, так называемые "индийские", но в наших краях это очень редкий гость, да и качество говорят у них не очень, поэтому такой вариант не рассматриваю.

Но у меня цель установить стальной патрон по типу k01-50. Так как у этого патрона посадочная резьба М14х1, то накрутить его на штатный шпиндель не получится, поэтому будем менять и шпиндель, с увеличением проходного диаметра, что так же очень важно. Корпус моторного блока останется штатный.

Отдельную благодарность хочу выразить Владимиру и Ведимиру с телеграмм канала мини-станки за подарок в виде этого шпинделя, он очень пригодился и пошел сразу в дело. Без них данная доработка не состоялась бы в таком виде.



Маркировка шпинделя D15-125-M14x1, что означает внешний диаметр 15 мм, длина вала 125 мм, резьба М14х1, проходное отверстие 9 мм. Первая проблема это требуется замена подшипников, и можно купить подшипник типоразмера 15267 2RS (15x26x7 мм), но это велосипедные подшипники с низким качеством изготовления и с довольно довольно большими люфтами. Как выяснилось далее что этот вариант на самом деле вполне хорош - из за качества изготовления моторного блока в целом - люфт в подшипнике здесь помог бы. Но я пошел другим путем, мне хотелось обеспечить наибольшую жесткость и точность в узле. Искал роликовые, а лучше конические подшипники, но никаких подходящих типоразмеров не нашел - посадочное место в крышке моторного блока диаметр 26 мм, глубина 8 мм. Но нашел бессепараторные двухрядные шарикоподшипники, такие то же устанавливаются в шпиндели станков, типоразмер 3802 (я купил FUSHI 3802-2RSV 15x24x7). Да, внешний диаметр у них 24 мм, а нужен 26 мм, придется изготовить пару переходных колец на внешний диаметр, но это не беда. Подшипник хорошего качества, но внутри смазан белой тефлоновой смазкой, которая не подойдет под наши цели, она для больших поперечных нагрузок, но под малые скорости качения. Вымываем ее и забиваем литолом (я наполнил специальной смазкой для высокоскоростных подшипников, но я не советую вам так делать, она все таки довольно густая и сопротивление качению создает изрядное, поэтому в данном случае лучше обычный литол - у нас нет таких скоростей что бы понадобилась специализированная смазка).



Подшипник изготовлен в минус пару соток, я решил не протачивать вал (это практически нереально не имея круглошилифовального станка или без возможности проточить в центрах на высокоточном станке, использование наждачки испортит геометрию вала гарантировано). Буду шлифовать внутренее кольцо подшипника. Для этого на 3Д принтере была изготовлена оправка для зажатия внутреннего кольца подшипника, после этого зажав его в станок кусочками мелкой наждачной бумаги P1000 шлифуем внутреннюю поверхность кольца поджимая наждачную бумагу с помощью палочки, контролируя по калибру - штихмасу, который был настроен на 15.00 мм по губкам штангенциркуля. Здесь нужно контролировать плотность захода калибра. На конечных этапах я контролировал хвостовиком шпинделя. Задача была добиться плотной посадки, но с сильным давлением от руки. У меня это заняло примерно полтора часа на оба подшипника. Модель кондуктора можно  [скачать здесь stl](/3d/Проточка-подшипников-1.stl) и [исходник в FreeCAD](/3d/Проточка-подшипников.FCStd)




Следующим этапом изготовил внешнее кольцо 26 мм внешний диаметр, 24 мм внутренний. Использовал алюминиевую трубку, это дешевле чем покупать болванку дюрали нужного диаметра и спускать ее в стружку. Стоит сказать что когда мы говорим о посадках это всегда ловля сотки или даже микроны, нужно быть готовым к этому, иметь соответствующий измеритель. Тут нониусным штангенциркулем с ценой деления 0.1 мм ничего не сделать, нужен хотя бы цифровой среднего ценового сегмента с разрешением 0.01 мм. Из доступного в домашних условиях можно использовать калибры (тот же штихмас), но эти способы измерения требуют хорошей чувствительности рук что бы ловить плавность хода калибра. Посадки можно делать наждачной бумагой с мелким зерном, но нужно учитывать что это финальная тонкая подгонка, использование шкурки в любом случае будет влиять на геометрию (будут закругляться края например).



Еще есть проблема с ременной передачей, ведь стандартный шкив с отверстием на 10 мм, а нужен на 15 мм. Пошел по простому пути - напечатал необходимую шестеренку на 3д принтере. Это скорее всего временный вариант и нужно переходить на другой тип ремня. Модель [скачать здесь stl](/3d/Шестерня-шпинделя.stl) и [исходник в FreeCAD](/3d/Шестерня-шпинделя.FCStd)

И так у нас все готово! Надеваю подшипник на вал шпинделя, на подшипник надеваю расширительное кольцо и вставляю все это в корпус моторного блока. То же самое делаю с задним подшипником. Закрепляю на хвостовике шпинделя напечатанный шкив. Включаю, и сразу получаю проблему - очень сильно греются подшипники, шпиндель подклинивает. Оказалось что крышки моторного блока не параллельны между собой и общей оси центровки нет, а за счет того что я выбрал двухрядные подшипники они очень жесткие и требуют строгой соосности переднего и заднего подшипников в их корпусах. Разбираем все) Нужно протачивать посадочный диаметр передней крышки, тот диаметр которым она садиться внутрь корпуса моторного блока. Диаметр в который садится подшипник - не трогаем! Передняя крышка после проточки не будет настолько плотно садиться, поэтому у нее появится определенный люфт, который позволит скомпенсировать общую неравномерность геометрии корпуса блока и задней крышки.



И так собираем все заново. И теперь ничего не греется. Это успех.



Просверлю хвост шпинделя, через него удобно затягивать патрон на шпинделе, вставив просто отвертку в отверстие. Такое отверстие было на штатном шпинделе и я им постоянно пользовался. Сверлю через кондуктор в виде неудачно напечатанной шестеренки, предварительно сделав сквозное отверстие в ней по центру.



Накручиваю патрон, замеряю биения.. и они порядка 0.05 мм, что для меня многовато. Посадочный поясок под патрон на шпинделе диаметром 14.00 мм, а в патроне 15.00, разумеется никакой центровки патрона не будет. Сделаю здесь кольцо посаженное на плотную посадку под запрессовку, а дальше проточу это кольцо прям на шпинделе до 15.00 мм, ловлю посадку накручивая патрон. 




После этой процедуры опять закручиваю патрон, капнул масла на центрирующий поясок, что бы патрон не так его натирал при закручивании. Измеряю биение - совсем другое дело, порядка 0.02 мм как торцевое так и осевое, это меня устраивает.



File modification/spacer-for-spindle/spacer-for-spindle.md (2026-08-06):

# Проставка 25 мм под шпиндель передней бабки токарного станка

Штатный кубик-проставка высотой 25мм и габаритами 50х50 мм под шпиндель представляет собой литой полый кубик довольно сложной геометрии с тонкими стенками, разумеется, никак не обработанный после литья. С ним есть ряд проблем:
* Кривая геометрия. Можно выровнять его плоскости (что довольно проблемно из-за их малой толщины).
* Крепление к балке и моторному блоку через распорные клинья, которые, как их ни дорабатывай, будут хоть немного, но отгибать в сторону верхнюю часть относительно нижней (проставку относительно балки).
* Недостаток точек крепления: по сути, это одна точка через центральные клинья (да, еще есть усиливающие пластины по бокам, но они никак не завязаны с проставкой, расстояние между точками крепления балки и моторного блока там слишком большое - 75мм). При сильной затяжке довольно тонкую стенку балки начинает выгибать - уходит плоскость соприкосновения и появляется эффект раскачивания на этом возникшем бугре, а так как точек крепления мало, выбора особо нет: зажимать надо надежно.
* Нет возможности выставления оси шпинделя по горизонтали. Выяснилось что параллельность стенки моторного блока не дает соосности оси вращения шпинделя относительно движения продольной подачи. Сам шпиндель внутри моторного блока установлен не строго параллельно стенке блока. В штатном варианте это можно решить с помощью подкладок из фольги между корпусом моторного блока и усиливающей планкой сбоку.
* Низкая жесткость закрепления из-за малой площади соприкосновения. Сам моторный блок имеет размер 75х50, но проставка всего 50х50, то есть треть площади моторного блока не задействовано в закреплении и висит в воздухе.

Автор YouTube-канала Игорь KLIV также боролся с проблемой крепления передней бабки: он использовал две штатные проставки, залитые эпоксидной смолой с примесью металла. Также он распилил еще одну малую проставку высотой 25 мм пополам и получил две половинки, которые с помощью шпильки присоединил к штатным проставкам, увеличив их плоскость до 75х50. Сделал поверхность ровной путем фрезерования. Моторный блок он положил на бок, дополнительно используя еще проставку 50 мм (кусок стандартной балки) для опоры второй проставки. Получилось достаточно массивное основание с большим количеством креплений. Это позволит получить неплохую жесткость, задействовать много точек крепления и распределить нагрузку от затяжки винтов на много точек. Здесь же есть несколько минусов: придется иметь несколько проставок (3 шт по 25 мм, и 1 на 50 мм), множество клиньев для стяжки блоков между собой, несколько боковых усилителей. Это дорого. Эта конструкция достаточно сложно настраивается, чтобы все располагалось параллельно ходу резца как вертикально так и горизонтально. По сути, конструкция является несъемной, что для меня самый большой минус, ведь снимать переднюю бабку мне нужно регулярно для работы с фрезерным вариантом станка (фрезерная колонна, особенно горизонтального фрезера несовместима с передней бабкой токарника). Некоторые варианты, которые делают, предусматривают сверление балки и моторного блока и жесткую стяжку шпильками всей конструкции, что также делает конструкцию несъемной; по сути, станок становится не модульным. Мне хочется оставить изначальную модульность станка.

Идеи которые были заложены в мою конструкцию проставки:
* Простая конструкция и простое изготовление. Например, отсутствие фрезеровки внутренних "ласточкиных хвостов".
* Нет креплений через распорные клинья
* Возможность регулировки по горизонтали для настройки параллельности оси вращения и подачи.
* Быстросъемная конструкция (здесь идея сделать фрезеровки для сдвижки верхней части проставки родилась не сразу, поэтому на фото там отверстия).
* Большое количество точек крепления.
* Большая площадь поверхности соприкосновения 80х50. Да, проставка на 5 мм будет больше, чем длина моторного блока. Это необходимо для доступа к заднему ряду винтов крепления двух половинок.
* Крепление через штатные пазы в балке и моторном блоке без дополнительного их сверления.
* Высокая жесткость конструкции.
* Режим поворота передней бабки по своей оси для точения конусов (эта идея в итоге убрана; именно поэтому в фото и описательной части можно заметить некоторые расхождения: в конструкции есть, например, отверстие в центре под ось вращения, есть пара дополнительных отверстий в верхней части проставки для механизма фиксации в повернутом состоянии) - при повторении этого делать не надо.
* Совместимость с отверстиями с шагом кратным 8 мм (эта идея добавилась в конце; она для совместимости с креплением продольной подачи сверху проставки, например, для использования ее в вертикальной подаче фрезера; опять же, тут есть некоторые расхождения с фото из-за того, что дополнительные 4 отверстия были добавлены позже).

Приступаю к делу! Сначала всё спроектировал в CAD системе (я использую FreeCAD), распечатал на принтере и проверил совместимость проставки на реальном станке. Проставка из двух половин: на 3D модели они по 12.5 мм каждая, в реальности продаются заготовки по 12 и 14 мм, а по 13 нет). Поэтому проставка будет из неравных по толщине половинок: одна 12 мм (нижняя), другая 13 мм (верхняя).

Распиливаю заготовку из Д16Т на горизонтальном фрезере.



Фрезерую торцы, загоняю в размер 80х50 обе заготовки. 



Вывожу нижнюю плоскость на верхней части проставки (этой плоскостью она будет соприкасаться с верхней стороной нижнего блока). Также вывожу обе плоскости на нижней части. Использую поверочную плиту и шабер. Добиваюсь равномерного рисунка по всей поверхности, без фанатизма. Это, конечно, необязательный этап, и можно было выровнять фрезерованием с минимальным съемом или просто шкуркой на ровной поверхности.



Размечаю верхнюю поверхность верхней части. Здесь важна точность разметки. Предпочтительный способ разметки - штангенрейсмас. На тот момент я делал это с помощью разметочного штангенциркуля - получается хуже: нужно хорошо контролировать перпендикуляр между штангенциркулем и размечаемой поверхностью, иначе размеры уплывут в "в минус" от требуемых.



Далее зажимаю в тисках и сверлю центральное отверстие (технологическое). Через него заготовки будут стянуты друг с другом, и дальнейшая обработка будет идти пакетом сразу двух заготовок, для того чтобы не иметь проблем с соосностью отверстий между нижней и верхней половинками. На самом деле это отверстие задумывалось как ось вращения для поворота половинок между собой для точения конусов. Но идея не прижилась, поэтому можно это отверстие не сверлить, а приступать к следующему шагу.



Крепим две половинки болтом друг к другу, зажимаю обратно в тиски. Не трогаю поперечную подачу - сверлю насквозь 4 отверстия, идущие по центральной оси, сверлом 4мм. 
Далее открепляю верхнюю и нижнюю части. На верхней части просверливаю два дополнительных отверстия 4 мм на центральной линии. Разумеется, всегда применяю центровку для каждого отверстия, это принципиально важно для точности сверления.



Следующим шагом на внутренних поверхностях обеих частей нужно сделать углубления диаметром 8 мм и глубиной 5 мм для шляпок болтов (я использую имбусовые болты под шестигранник, но можно, например, использовать болты с тонкой шляпкой, там глубины фрезеровки хватит и 2мм). Лучше всего использовать специальный инструмент - цековку; это специальная фреза с направляющей (цапфой), тогда отверстия получатся идеально по центру. За неимением я делал просто фрезой ф8.

Опять закрепляю две половинки друг к другу болтами, и можно сдвинуть каретку поперечной подачи для сверления боковых отверстий. Причем, так как левый и правый ряды отверстий находятся на одинаковом расстоянии от торца, можно просто перевернуть заготовку на 180 градусов, чтобы просверлить другой ряд отверстий. Смещать каретку не нужно. Сверлю 4 отверстия сверлом 3,3 мм насквозь (под резьбу М4 на нижней части в будущем).

Снова открепляю половинки и на верхней части делаю фрезеровку для крепления под шляпки болтов. На нижней части нарезаю резьбу М4, прямо в станке. Это позволяет первые витки нарезать ровно. Пользуюсь обязательно олеиновой кислотой (продается в любом интернет-магазине, интернет-барахолке, или оффлайн-магазинах). Дорезать резьбу буду шуруповертом потом, в снятом со станка состоянии. Рекомендую также перед нарезанием резьбы пройти отверстия зенковкой, это поможет сверлу встать вертикально, а выдавливаемый материал как раз заполнит ямку от зенковки и не будет выпирать над поверхностью.



Далее смещаем каретку и просверливаем дополнительные 4 отверстия по центру (это для совместимости с креплениями под шаг кратный 8 мм). Если вы не собираетесь использовать проставку нигде, кроме передней бабки, эти отверстия вам не пригодятся, и можно пропустить данный шаг.

Теперь можно фрезеровать два поперечных паза на верхней плоскости верхней части. На самом деле этот паз необходим только спереди - там болты с внешним шестигранником, и приходится работать с ними рожковым ключом, но для симметричности фрезерую такой же паз и сзади.



Следующим шагом нужно довести высоту проставки ровно до 25 мм. Закрепляем две половинки друг с другом и фрезой-летучкой фрезеруем верхнюю поверхность до требуемого размера.



Почти все готово по самой проставке: нужно просверлить и нарезать резьбу М4 в торцевых частях обеих половинок проставок. Ну и готовый результат.



Если у вас есть достаточное количество стандартного крепежа для фиксации, можно воспользоваться им - потребуется двойных 6 гаек и 4 одинарные для фиксации на балке. Короткие усиливающие боковые пластины придется в любом случае сделать из полосы алюминия.
Но я решил изготовить длинную гайку с 6 резьбами из куска латуни.
Распиливаю заготовку на горизонтальном фрезере.



Распечатал кондуктор для зажима заготовок в тисках под 60 градусов и фрезерую в нем торцы заготовок.



Сверлю отверстия 3,3 мм по центральной линии заготовки. Нарезаю резьбу по месту, используя в качестве кондуктора саму проставку, прижав их друг к другу в тисках.



Ну и последнее: надо изготовить 4 одинаковых усиливающих боковых планки. Их изготовил из полосы АМГ3 толщиной 5 мм. Там все просто: сверлим 4 отверстия с расстоянием 25 мм между центрами для стандартных двойных гаек.



И вид в сборе: 




Сборка производится в следующем порядке:
* Закрепляем верхнюю часть проставки на моторном блоке, причем моторный блок должен быть смещен слегка вперед, так чтобы шлицы задних винтов были доступны для вкручивания.
* Закрепляем нижнюю часть на балке. Из-за тонких стенок балки важно как не перетянуть винты, чтобы балку не выгнуло, так и закрепить боковые усиливающие элементы, иначе при нагрузках на моторный блок его будет неизбежно отгибать в сторону.
* Вкручиваем передние два болта.
* Надвигаем моторный блок с проставкой вперед на эти болты.
* Закручиваем задние винты.
* Регулируем соосность оси шпинделя и продольной подачи и зажимаем все винты и болты. Разборка производится в обратном порядке: начиная с задних винтов, затем можно сдвинуть весь блок вперед, выкрутить передние винты до конца и сдвигом назад отсоединить моторный блок с верхней частью проставки.

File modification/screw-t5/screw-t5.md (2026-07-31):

винтовая пара на станке с завода состоит из шпильки м6 и латунной втулки вставленной в каретку на посадке. Разумеется эта крепежная шпилька не предназначена для постоянных перемещений, поэтому постепенно пропиливает латунную резьбовую вставку, в результате сильно увеличивается холостой ход винта (люфт) и в конечном итоге происходит срыв резьбы. Что у меня и произошло.
Я заранее подготовился и купил ходовую пару винт т5х1 и гайки к нему. Все это продается в магазинах торгующими запчастями для 3D принтеров и ЧПУ. Профиль резьбы на этом винте специально создан для перемещений, сам он шлифован и не будет так сильно истирать латунную гайку.
Придумал два варианта как внедрить гайку т5 внутрь каретки. Первый вариант нарезать внешнюю резьбу м8 на гайке т5, ну и в самой каретке нарезать внутренюю резьбу и вкрутить вставку-гайку на резьбу. 
Попробовал такой способ, начал с нарезания на латунной гайке внешней резьбы плашкой м8. И тут меня ждало фиаско. Материал из которого изготовлена гайка это латунь сыпучка (лс-59), она не режется, а крошится, очень твердая, резьба получается рваная, а стенка между внешней и внутренней резьбой меньше миллиметра. Кроме того резьбу в ручную ровно нарезать очень очень сложно, получается с перекосом, а это недопустимо, винт будет ходить с перекосом то же. В общем я решил что вариант тупиковый.
Второй вариант рассверлить отверстие в каретке до 8мм (внешний диаметр латунной гайки т5 как раз 8мм), дальше отфрезеровать паз губиной 3мм для новой вставки, просверлить крепежное отверстие под болт м3. Саму втулку надо отфрезеровать, убрав лишнее с фланца. Должно остаться одно "ухо" с отверстием через которое и будем крепить на каретку. На фото показан процесс изготовления и финальный результат.
Такой способ доработки каретки и внедрения вставки т5 показал себя с наилучшей стороны, получившаяся втулка вставляется очень плотно, дополнительно надежно фиксируется на болт (пробовал выбить оттуда при затянутом винте, не получается, сидит отлично). Все это легко получилось сделать ровно, даже с учетом что я сильно спешил. На этом первая часть внедрения ходового винта т5 закончена. Во второй части останется проточить сам ходовой винт, нарезать резьбу и сделать лыску под стопорный винт.
Продолжение перевода каретки на винт т5: с одной стороны ничего сложного, требуется проточить винт до диаметра 4.00 (в плюсе 5 соток), нарезать резьбу м4 под прижимной винт ручки, и снять небольшую лыску под ручку. Однако здесь важна последовательность (технологическая карта так сказать). 
Во первых нужно на минимальном вылете проточить винт до диаметра 3.9-3.8мм под резьбу, первые с краю миллиметра 4 я рекомендую просадить до 3.6-3.5, так заход плашки будет плавнее и ровнее, так же не забываем снять фаску. 
Далее самый сложный этап - нарезание резьбы, сталь тут довольно крепкая, проворота винта в тисках не избежать, для уменьшения последствий я зажимал через лист латуни, да это во многом помогло, но зажиматься тисками нужно как можно ближе к самой нарезаемой резьбе, эту испорченную часть все равно будем протачивать - не жалко. И на этом этапе я убил свой первый винт, загубил основную резьбу (благо у меня их два было).
Третьим пунктом в нашей технологической карте проточка винта дальше за резьбой на длину 23мм, диметр 4.00 (в плюсе 5 соток). С этим достаточно просто, только хорошо бы иметь регулятор оборотов, для стали 3000 об/мин на шпинделе очень очень много, стружка горит. Желательно 1000-1500.
Следующим этапом я отполировал наждачкой 1500грид прям в станке получившуюся ось, так как эта часть будет находиться в паре трения и нам тут шероховатость и заусенцы не нужны.
Ну и самое последнее - лыска. Делал бормашинкой с отрезным кругом, зажав в тисках через латунь сам вал и приставляя диск боковой частью к валу и постоянно примеряя ручку когда она будет входить. Получилось вроде неплохо. Благо в этой лыске точность не нужна.
Ну и все винт готов! Осталось самое приятное, сборка, настройка, смазка. Результат на фото. Получился очень плавный мягкий ход каретки. Холостой ход в паре гайка-вал (а он всегда будет и это правильно) - 2 деления по лимбу (0.08мм). 
Самое большое преимущество данной конструкции - простая смена гайки при необходимости (а необходимость в любом случае появится, как не старайся, а трение никто не отменял, просто ресурс трапецеидальной резьбы сильно больше, но и он конечный). Гайка изготавливается из обычной гайки т5х1 от 3д принтера, хоть ножовкой, хоть бормашинкой, просто отпиливанием лишней части фланца, отверстие используется штатное. Размер уха произвольный, лишь бы залезло в место в каретке. Гайки эти общедоступны и дешевые, можно наточить их заранее, меняются при надобности выкручиванием одного болта.
Доработку рекомендую, получилось неплохо, посмотрим как покажет себя в эксплуатации
Ну и в заключении темы перевода кареток на винты т5 внедрил гайку т5 в малую каретку.
1. Надо выбить штатную втулку, закрутил длинный болт м6 с обратной стороны и легким ударом молотка по болту втулка спокойно вылетает.
2. Надо выставится по центру отверстия, лучше это сделать с помощью фрезы 7мм, она почти входит в штатное отверстие (оно сделано на десятку в минусе).
3. Поднимаем вертикальную подачу и меняем фрезу на 8мм и фрезеруем в глубину, до вылета фрезы со стороны центрального паза.
4. Не трогая ручку поперечной подачи чтобы не смещать центр фрезеруем выборку глубиной 3мм под ухо гайки т5
5. Теперь займемся самой гайкой, которую надо отфрезеровать с 3х сторон, оставив только крепежное ухо. Тут главная проблема что бы отверстие получись строго по центру уха. Ширина уха 7.9мм, длину уменьшать не надо.
6. Далее надо скруглить получившийся квадрат от фрезеровки до диаметра 8мм или чуть меньше, главное что бы оно пролазило в ответную выемку. В прошлый раз я сделал это бормашинкой от руки. Сейчас я решил попробовать закруглить этот угол зажав в тисках кусок шпильки т5, накрутив на нее гайку, держа за ухо пассатижами приближая к фрезе и делая вращательные движения, тем самым снимая углы. На фото видно. Получилось отлично, очень ровное закругление нужного диаметра. Технологию можно брать в копилку.
7. Ну и вставляем гайку в каретку, сверлим отверстие по месту под фиксирующий винт. В данном случае я решил попробовать винт м4 (все таки м3 на мягких материалах типа алюминия имеет слишком мелкий шаг). Сверлим отверстие диаметром 3.3мм, нарезаем резьбу м4. Делаем в самой гайке фаску под потай болта. Ну и вкручиваем болт. Шляпка болта не мешает винту подачи, все нормально, можно так делать.
Кажется что получилось аккуратнее чем с прошлой кареткой, времени было больше. Держится такая вставка отлично, стоит в идеально ровно. Изготовление ходового винта аналогичное как для продольной подачи, что я уже показывал, тут только длина ходового винта будет меньше.
Буду потихоньку переводить все свои малые каретки на винты т5, они показали себя с лучшей стороны.
























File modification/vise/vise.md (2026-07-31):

# Доработка тисков

Точность обработки деталей зависит не только от геометрии станка, но так же от инструмента - тисков. Насколько крепко они могут зажать заготовку, насколько будет поднимать заготовку при зажиме, насколько хорошо их плоскость прилегания к фрезерному столу парралельна внутренней плоскости тисков. Со станком идут простенькие тиски изготовленные методом литья без какой либо обработки, из цинкового сплава. В целом почти год работы с ними показал что они имеют право на жизнь, но сразу же вылез ряд проблем не позволяющий хорошо зажать деталь. Проблемы: 
1. Поверхности прижима тисков к станку не обработаны и кривые после литья. Отсюда что даже хорошо выставленная геометрия шпинделя к кареткам нарушается тисками, так как внутренняя поверность тисков не паралельна внешней у основания.
2. Губки как подвижная так и неподвижная не под 90 градусов к основанию тисков, тем самым прижимая деталь она стремится прижаться к губкам, но тут же отжаться от основания (на фото с лекальным угольником видно что зазор сверху есть, а снизу нет, то есть угол больше чем 90 градусов)
3. Подвижную губку сильно выворачивает при зажатии, причем выворачивает как вертикально, так и горизонтально. Когда мы зажимаем деталь ближе к концу губки, тогда происходит выворот подвижной губки в горизонтальной плоскости, тем самым деталь зажимается не всей поверхностью, а только углом, такое зажатие ненадежное.
При вертикальном вывороте деталь со стороны подвижной губки поднимает вверх, замерил щупами - примерно на 0.15мм (на 30мм детали). На фото видно как сильно поднимает заготовку со стороны подвижной губки.
Это происходит по причине что прижимной сухарь подвижной губки очень короткий, никак не фиксируется ни в пазе котором он ходит, на на самой губке, кроме как одним болтом, и его свободно разворачивает в любую сторону. Сама ширина губок 10мм, что очень мало конечно, но с этим ничего толком не сделать. Но и тиски не лекальные.




Решил тиски доработать:
1. Отфрезеровать все рабочие поверхности, придав им нормальную геометрию
2. Сдалать новый сухарь подвижной губке, совершенно другой конструкции.

Первое что надо сделать это выравнивание поверхностей базирования самих тисков на каретке, так и деталей в тисках. Разумеется делать надо после того как мы уверены в геометрии станка, что шпиндель точно вертикально стоит относительно каретки как продольной так и поперечной подачи, иначе сделаем тискам только хуже.
Начинать нужно с фрезеровки наружных поверхностей. Я зажал тиски перевернув их прям за каретку и выставившись по индикатору. На фото видно метод зажатия на каретке и результат фрезеровки. Можно было прижать их через штатные отверстия болтами и профрезеровать внутренние салазки по которым ходит сухарь подвижной губки. 



Далее прижимаем через подходящий кусок пластины или через штатный сухарь тиски к каретке и фрезеруем плоскость прилегания тисков к каретке.



Далее можно переходить к фрезеровки внутрненних поверхностей. Начинаем с неподвижной губки, выставляем тиски обкатывая по индикатор по неподвижной губке, фиксируем тиски и фрезеруем.



К сожелению хода поперечной подачи не хватает что бы отфрезеровать заднюю поверхность тисков (там где винт) без перестановки тисков, а без этого не получится фрезеровать подвижную губку. 
Откручиваем тиски, разбираем, выкручиваем прижимной винт, ставим тиски наоборот, обкатываемся индикатором по только что фрезерованой неподвижной губке, и фрезеруем противоположную часть там где винт.
Сьем с поверхностей получился минимальный - менее десятки. Так же интересное фото фрезеровки передней губки, где видно что на первом проходе берет только снизу, из за наклона самой губки.



Так как я собираюсь делать полностью свой новый сухарь к подвижной губки, то проточка подвижной губки должна быть уже с новым сухарем. Поэтому делать ее буду в самом последнем этапе.
Вроде работы не много по фрезеровке рабочих поверхностей тисков, но куча перестановок и обкаток по индикатору муторно и долго конечно. Дополнительно я притер к поверочной плите нижнюю поверхность тисков после фрезеровки, в принципе не обязательно, но раз у меня есть возможность, то почему бы и не сделать.

Вторым этапом после фрезеровки поверхностей тисков будет изготовление сухаря прижимающего подвижную губку к корпусу тисков. В длину деталь будет равна ширине подвижной и неподвижной губок + задняя отливка = 30мм, ну а шириной внутреннего паза - 25мм, высота 9.5мм. На фото чертеж детали сухаря.



Первым делом фрезеруем базовую нижнюю поверхность заготовки, в размер 9.5мм по общей высоте заготовки.
Во вторых ставим заготовку на эту базовую поверхность, я использовал как обычно плитки КМД в качестве паралельки и фрезеруем две ходовых поверхности, которыми сухарь будет скользить по телу тисков, от верхнего края у меня получилось 5мм глубиной и 4мм шириной. Данные размеры подгонялись под конкретные  тиски, по месту, поэтому увы снятия тисков и примерок не избежать. И снова выставление тисков по индикатору и снова фрезеровка.



Третьим этапом фрезеровка верхней поперечной выемки куда будет вставать подвижная губка, шириной 10мм, глубиной 2.5мм.



Ну и последнее - отверстие для фиксирующего болта ровно по центру (хотя возможно его надо делать первее предыдущего этапа и фрезой позиционироваться относительно этого отверстия). На задней стороне сухаря у отверстия нужно сделать зенковку под потайной болт.




Сухарь закончен, получилась достаточно точная деталь, удалось "ловить сотки" при подгонке по месту, итоговый вид на фото.



И последний этап доработки тисков это фрезеровка подвижной губки.
Для начала нужно отрфезеровать плоскость сопрягаемую с прижимной гайкой, здесь просто переворачиваем губку и прижимаем ее к неподвижной.
Далее собираем полностью тиски, выставляемся по индикатору по неподвижной губке. Я использовал 2 плитки кмд для того чтобы упереть в них неподвижную губку и винтом тисков зафиксировать ее как на картинке. Фрезеруем плоскость подвижной губки снимая минимальный слой. 



Тиски готовы.

Зажал плитку кмд в тисках и померил отжим плитки с помощью щупов, отжима практически не стало, либо он стал сильно меньше (тут стоит сказать что результат не всегда повторяем, но однозначно намного лучше чем было). Удается зажать плитку кмд что бы щуп 0.02 не лез, это конечно прекрасный результат, но результат нестабильный. Стабильный результат в районе 0.05мм отжим от поверхности тисков что все равно в 2-3 раза лучше чем было по заводу. Так же на последних фото видно как не перекашивает подвижную губку при зажатии не по центру - с этим результат отличный, но сильно зависит от качества изготовления поджимающего подвижную губку сухаря.
В итоге: тиски конечно лекальными не стали, но качество зажатия заготовок однозначно повысилось. За неимением нормальной альтернативы штатным тискам для этого станка вариант немного доработать штатные вполне - неплохой.



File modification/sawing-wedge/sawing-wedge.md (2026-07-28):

# Распиливание разжимных клинов

Модульность - одна из главных фишек станков конструкторов, когда можно собрать из кубиков нужный тебе вариант станка сейчас же, лишь бы было достаточное количество деталей. Она же один из главных минусов. отражается это в том что все кубики прижимаются друг к другу распирающими прижимами, в купе с тем что все кубики это либо литые детали либо экструзионные без постобработки, то разумеется они не имеют хорошей геометрии. В результате имеем плохую геометрию станка из коробки. Прижимы имеют изначальный дефект - всего один разрез, тем самым создается не только распирающее усилие, но и крутящее в лево-право по горизонтали, поэтому не удается выставить все кубики-балки соосно друг другу. 



На канале Игорь KLIV найдено видео https://youtu.be/zCfJStTneY0?si=hLFgV2koFm3BTt6X с решением этой проблемы, распиловкой на несколько частей, таким образом расширяющее усилие не имеет крутящего момента. Решил модифицировать и свои прижимы таким же образом. В видео Игорь пилит свои прижимы лобзиком, в ручную отпилить ровно очень сложно и требуется постобработка, с дальнейшей шлифовкой. 

Я решил почему бы не отпилить на этом же станке отрезной фрезой. Что и было сделано. На фото разметка деталей, просто прижав друг другу со смещением в тисках, контролируя что обе детали прижаты к нижней поверхности тисков, таким образом получаем нужный угол реза. Предварительно стороны деталей надо зачистить удалив облой от литья, который будет мешать ровному зажатию.





Пилил отрезной фрезой 40х0.2, зажав прям на каретке прижимом, в этот раз использовал лесенку, так было удобнее. Такой способ зажима использовал потому что поворотного блока у меня нет, а прижим позволяет получить любой угол реза. Первую половину толщины пилится легко, а вот во вторую половину начинаются проблемы, из за большого заглубления фрезы, она начинает очень быстро затирать, разогреваться, разогревать деталь. Тут бы помогло большое количество СОЖ, но это не тот станок. Сбрызгивал WD-шкой и пилил с перерывами на остывание. UPD: перешел в последствии на изопропиловый спирт, он намного лучше отводит тепло от детали и фрезы, стружка не маслянная и не разбрасывается по сторонам, спирт сам легко высыхает не оставляя следов, рекомендую.



Распилил в 4 прохода. Рез гладкий, ровный, не требует обработки, разве что края прошелся надфилем, а то больно острые получаются. Уголки детали срезал просто на глаз, зажимая в зажим на ластохвосте и отмечая лишнее, порядка 5мм. Ну и на фото после модификации все ровно, кубики не разворачивает. Почему китайцы не делают так из завода непонятно.




Дополнение по эксплуатации: все равно разворот небольшой, но есть, это особенно заметно например при закреплении передней бабки или задней бабки где даже небольшой разворот кубиков между собой сильно заметен и сильно уводит центральную ось вращения шпинделя, но доработку я все равно рекомендую, ибо то что было и то что стало это небо и земля конечно.

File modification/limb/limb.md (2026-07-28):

# Поворотные лимбы для каретки

Лимб важная часть станка, по нему ориентируемся когда нужно передвинуть каретку на определенную величину, проточить на определенную длину и тд, то есть любые фрезерные и токарные работы которые не на глаз, а по размерам требуют работу с лимбами. Штатные лимбы плотно сидят на ручке подачи и не вращаются, работать с ними неудобно, выставить на ноль нельзя, и приходится в голове делать операции вычитания или сложения, легко просчитаться и ошибиться, особенно когда домашние отвлекают. Хотя замечу что на лимбе есть накатка, что как бы наталкивает на мысль что лимб должен двигаться рукой, но кажется что ради удешевления решили этого не делать. Еще имеется проблема люфта, дело в том что тело ручки сделано методом литья и посадка винта в ручке очень не плотная, предполагается выбирать люфт затяжкой винта на валу подачи, но этот способ по факту не рабочий - затягиваем винт - убираем люфт - добавляем сопротивления на трении, становится сложно крутить ручку, затягиваем клин на подаче - начинает проскальзывать ручка - опять затягивай гайку в ручке, бесконечный круг. Еще проблема что между ручкой и кареткой стоит обычная шайба, типа подшипник скольжения, скользит разумеется плохо, особенно если забивается стружкой. В целом все это устранимо.

Цели доработки: 
1. Установить упорный подшипник вместо шайбы
2. Сделать фиксирующий винт в ручку что бы при любой затяжке гайки люфта в узле винт-ручка не было.
3. Сделать поворотный лимб на ручке подачи.

Для реализации самое главное соблюдать очередность этапов работ: 
1. просверлить сквозное отверстие 2.5мм напротив лыски ручки, нарезать резьбу м3
2. Просверлить отверстие 2.5мм на глубину 2.5мм
3. Ножом сбить лимб с ручки
4. Нарезать резьбу м3 в лимбе для винта фиксации лимба на ручке
5. Шкуркой шлифануть посадочный диаметр ручки что бы лимб свободно вращался.
6. Отфрезеровать на ручке канавку глубиной 1мм и шириной 3мм
7. С торца ручки отфрезеровать отверстие 9мм на глубину 3.5мм.
   
Что же, план готов, технологическая карта так сказать, приступаем!
   
Сверлим отверстия, первое сквозное для зажима установочным винтом, нужно сверлить так что бы край резьбы пришелся в край накатки, сразу же нарезаем м3. Рядом сверлим отверстие под фиксатор лимба на ручке, так же 2.5мм на глубину 2.5мм, сама толщина лимба (красное кольцо) 2мм, то есть нам надо что бы сверло сделало небольшую ямку на самом теле ручки, это понадобится в дальнейшем. Центр отверстия должен быть в конце штриха на лимбе (3.5мм от края лимба). Правильное расположение ручки в тисках при этих операциях на фото. 



Дальше сбиваем ножом лимб, просто наставляем острие ножа между лимбом и маховиком ручки и легкими ударами молотка по ножу сбиваем лимб в посадки. 



Сразу же можно нарезать м3 резьбу в нашем отверстии под фиксатор лимба. 



Далее надо отшлифовать тело ручки, что бы немного уменьшить диаметр, так что бы лимб свободно вращался. Так как у меня есть поворотный блок и 4х кулачковый патрон я придумал насадить ручку на винт, отцентрировать в патроне по индикатору и вращая ручку отшлифовать



Далее надо нарезать канавку для пластикового кольца, в него будет упираться стопорный винт лимба, а кольцо будет прокручиваться, затяжкой винта можно будет регулировать усилие вращения лимба. Здесь нам пригодится небольшое углубление от сверления отверстия под стопор лимба, по этому углубления будем центрировать нашу канавку шириной 3мм и глубиной 1мм, центр канавки как раз центр углубления. Можно сделать это на токарном варианте станка, но на малых оборотах, надо регулятор. Я решил канавку сделать 3мм фрезой в поворотном устройстве, вращая руками ручку, и постепенно добавляя до глубины канавки 1мм, получилось отлично, проще и лучше чем резцом.



Далее я распечатал пластиковое кольцо со стенкой 0.8мм, хотя подошла бы латунная полоса шириной 3мм изогнутая кольцом.



Осталось установить тиски и зажать ручку сделать углубление под упорный подшипник, глубиной 3.5мм (сам подшипник толщиной 4мм) и диаметром 9. Центрировался по валу от принтера 6мм, вставляя в штатное отверстие. Пример фрезеровки и результата фото. 




По результату эксплуатации дополню: доработкой постоянно пользуюсь, вращающийся лимб это крайне удобно. Самое проблемное при изготовлении это сделать сделать канавку по которой будет ходить прижимное кольцо с винтом, надо сделать максимально точно, поэтому потратье время для выставления маховичка по центру перед тем как делать канавку.

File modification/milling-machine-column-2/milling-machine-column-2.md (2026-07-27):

# Крепление фрезерной колонны (новая версия)

Ранее использовал стандартный способ крепления колонны фрезера к основной горизонтальной балке станка через отверстия, просверленные насквозь в балке. Мне пришлось смещать колонну немного правее, и это вызвало сложности:
* Под новое место нужно фрезеровать новые отверстия в балке
* Достаточно хлипкие балки сильно ослабляются отверстиями
  
Поэтому решил пересмотреть всю систему крепления фрезерной колонны на станке, во-первых, отказаться от отверстий. Вместо того чтобы ослаблять места креплений, буду усиливать их. Также конструкция должна крепиться на станке через штатные «ласточкины хвосты» в балках, что позволит сдвигать колонну при надобности без переделок или, например, закрепить её на длинной балке 51 см.

Решил делать крепление на основе алюминиевого уголка 100х50х5. Увы, достаточно качественный нержавеющий уголок или хотя бы стальной мне найти не удалось: у всех, что мне попадались, внутренний угол был далеко не 90 градусов, а вот алюминиевые уголки продаются отличного качества с ровными 90 градусами (проверил по лекальному угольнику). Итак, нарезал несколько отрезков уголка: один 20 см (под размер продольной подачи) — это основа для закрепления подачи и основной балки станины, ну и с внешней стороны уголка будет крепиться колонна фрезера. Ещё пару уголков шириной 50 см: один под закрепление колонны сзади, второй под закрепление передней бабки. Остальной крепеж стандартный — двойные гайки в «ластохвост» и винты к ним. Рекомендую под винты подкладывать шайбы, чтобы не проминать алюминий.



Размечал штангенрейсмасом прямо на столе, удобно, гораздо удобнее, чем штангенциркулем. Ну и сверление большого количества отверстий — как правило, по месту. Обычно нужно просверлить одно отверстие, далее вставляем в него винт с двойной гайкой и отмечаем, где будет второе отверстие. Размечать по приборам бесполезно: у китайцев очень приблизительные размеры этих двойных гаек. Из интересного можно заметить пару моментов. Первое: две гайки крепления колонны (передняя и задняя) расположены вертикально, они усиливают колонну от качания вперёд-назад. Второе: заднюю гайку крепления удалось поднять на 50 мм выше, что, в теории, должно усилить крепление колонны. Ну и вид готового крепления до установки самого станка.



Сборку нужно вести в следующем порядке:
* Прикручиваем к основному уголку колонну как спереди так и сзади, затягиваем винты (спереди винты сделаны в потай)
* Легким постукиванием влево-вправо устанавливаем по угольнику вертикальный угол
* Затягиваем угловые усиливающие крепления на самой фрезерной колонне
* Задвигаем горизонтальную балку внутрь угольника и затягиваем усиливающие крепления от колонны уже на горизонтальной балке
* Контролируем угольником вертикальное расположение колонны относительно верхней плоскости горизонтальной балки
* Собираем остальные части конструкции станка



Ну и финальный результат станка с креплением на фото.



По результатам эксплуатации и замеров жесткости выяснилось что жесткость повысилась в разы, даже крупные фрезы типа ф8 и ф10 не вызывают вибраций и дробления. Про стандарные ф6 молчу - одно удовольствие, станок не напрягаясь режет под 3-4мм за проход д16т (для больших заглублений выбирайте либо двухзубые фрезы, либо шарошки типа "кукуруза"). Крайне рекомендую данную доработку для тех у кого фрезер. С этого надо начинать доработку фрезера пожалуй.

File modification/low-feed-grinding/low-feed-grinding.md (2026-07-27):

# Выравнивание поверхности ласточкиного хвоста малой каретки

Здесь видно как в середине ластохвоста имеется полоса от литьевой формы, проблема что когда место прижима клина винтом проезжает это место появляется смещение каретки.



Поработал немного надфилем, без энтузиазма, тут главное сбить горб и не навредить геометрии. По хорошему надо отфрезеровать это, но тут нужна фреза 60градусов и отлично выставленный станок, ни того ни другого у меня не было на момент доработки, поэтому фрезерованием сделаю только хуже. А вот надфилем, контролируя поверхность по лекальной линейке на просвет можно поправить этот узел (на фото). Ну и замер отклонения от перпендикуляра с латунным клином и поправленым ластохвостом. Результат 0.03 на 35мм подачи! И никаких виляний в 0.2мм что было раньше. А это я еще прижим клина после модернизации не настраивал. Но результат уже более чем устраивает. Такую доработку рекомендую однозначно, просто и эффективно.



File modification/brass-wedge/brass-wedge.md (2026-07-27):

# Латунный клин для каретки

В результате замеров выяснилось что малая каретка движется волнами, внимательно рассмотрев ластохвост каретки увидел что он был сделан на литьевой форме состоящей из нескольких частей, в месте их соединения неизбежно возникли неровности, то есть одна часть чуть выше другой. Так же в середине ласточкиного хвоста есть выборка под шляпку винта крепления. Штатный пластиковый клин прижимается несколькими винтами с острыми носиками прогибается в местах контакта, обрзуются волны на поверхности клина. При передвижении эта волны в местах прижима проваливаются в неровности на ласточкином хвосте, вот и получается что каретка как бы плавает по волнам, сильно страдает точность при перемещении поперечной и вертикальной подачи.
Что бы устранить этот эффект решил сделать латунный клин.

Для этого надо отфрезеровать под углом 60 градусов, и тут варианта 3:
* Использовать фрезу ласточкин хвост 60градусов,
* Использовать поворотное устройство и развернуть шпиндель фрезера
* Зажать деталь под углом.

Мне доступен только 3тий метод. Решил что отлично этому послужит сама каретка перевернутая вверх ногами, ведь там уже есть нужный нам угол 60 градусов, останется только сделать прижим любым доступным способом, с любой точностью по сути. Можно вообще использовать кусок шпильки\длинного винта или кругляк порядка 5мм. Но так как есть 3D-принтер был изготовлен пластиковый клин который поджимает заготовку к ластохвосту каретки и просто стальная полоса чтоб поджатие было равномерным. Поджатие производил через резьбы регулировочных болтов. 



Перевернул заготовку и отфрезеровал другой ее торец. 



И последнее - пазы для регулировочных винтов. Я вставил клин в каретку, затянул винты поджима, они сделали отпечатки на клине своими острыми носиками. Орентруясь по этим отпечатанным точкам делаю фрезеровку. На самом деле как показала практика фрезеровка эта лишняя и клин вполне себе хорошо сидит на месте и не сдвигается за счет этих углублений которые набивают прижимающие винты. Максимум что можно сделать зенковкой или тонким сверлышком чуть чуть углубить эти отверстия (не более 0.5мм) что бы прижимающий винт заходил чуть поглубже в тело клина.
Ну и результат на фото.




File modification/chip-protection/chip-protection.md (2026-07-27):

# Защита от стружки на шпиндель

Решил бороться со стружкой при работе отрезной фрезой и в целом для горизонтального фрезера. Спроектировал конструкцию из козырька и 2х направляющих закрепленных в штатных ластохвостах на фрезерной голове. Корпус защиты имеет вертикальный ход порядка 50мм, что более чем достаточно. Быстро снимается и регулируется. Дополнительной фиксации от сползания вниз не потребовалось, корпус в направляющих сидит с натягом. Еще прикрепил кусок пленки на правую сторону козырька, куда в основном стружка и летит, что полностью убрало стружку с правой стороны. В принципе после тестов могу сказать что теперь 90% стружки остается в зоне реза, на станке и не размазывается по всему столу. Остальные 10% улетают недалеко через неприкрытые места впереди, с левой стороны, сзади, но они все находятся не в плоскости движения фрезы и там стружка имеет малую скорость и падает рядом со станком и не мешает. Рекомендую такую доработку. 
В ходе эксплуатации выяснилось что данная конструкция довольно сильно заслоняет свет в месте реза, поэтому надо бы добавить окошко сверху которое затянуть прозрачным пластиком (например от бутылки). Так же неудобно подлезать в зону реза, например для уборки стружки или смачивания СОЖ, по хорошему надо бы добавить систему опрокидывания этого козырька.




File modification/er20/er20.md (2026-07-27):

# Переходник на цанговый патрон ER20

Для нестандартных задач, таких как фрезерование толстыми фрезами или отрезание в режиме горизонтального фрезера длинными оправками дисковых фрез, понадобилось изготовить переходник на патрон C25-ER20-50L с внутренним диаметром 16 мм. Такой патрон может зажимать цанги с отверстием до 16 мм, что более чем достаточно; также у этого размера патроны есть с диаметром 16 мм, что позволяет сделать переходник с резьбы М12 до диаметра 16 мм с достаточно толстой стенкой переходной втулки для надежного зажатия без деформации шпинделя или втулки.

Итак, первое, что делаем: отрезаем заготовку диаметром 20 мм, выравниваем поверхности проходным резцом. Сверлим отверстие 11,5 под внутреннюю резьбу М12х1. На станке такие отверстия сверлить не получится, поэтому сначала сверлю отверстие 6 мм, а далее растачиваю резцом до нужного диаметра, контролируя отверстие штихмассом как калибром.



Нарезаю внутреннюю резьбу М12х1; сделал комплектными метчиками из двух номеров, так режется проще, а резьба качественнее. Пользуюсь олеиновым маслом для нарезания резьбы.

 

Дальше нужно расточить внутренний конус 1:15. Для этого закрепил одну малую подачу на продольной подаче под углом 15 градусов к основной оси станка; использую меру угла 15 (на фото 20 и это ошибка) градусов и индикатор для контроля. Сразу скажу, что конус шпинделя выполнен не совсем качественно и, по всей видимости, не имеет строгого соотношения 1:15, а где-то немного меньшего угла, может, 14градусов, но измерить точно этот угол пока не представляется возможным. Правильным решением является выставление конуса по индикатору, ножка которого катается по поверхности конуса шпинделя. Расточка конуса оказалась вполне простым делом с малой продольной; единственным сложным моментом из-за нестандартного закрепления малой продольной стала высота резца — здесь пришлось поиграться с проставками под резцедержатель, чтобы добиться 50 мм от станины.

  

Дальше на фрезере необходимо выбрать две лыски под 17-й ключ, чтобы затягивать переходную втулку на шпинделе. Пока втулка стоит в патроне, дал риску на боковине втулки резцом на расстоянии 17 мм от центра. Снимаю втулку и на фрезере снимаю лыски до намеченной риски.



Теперь откручиваем патрон со шпинделя, накручиваем переходную втулку и затягиваем ее ключом. Осталась одна операция — очень точно проточить наружный диаметр до 16,00. Сначала по лимбу поперечной подачи проточил до 16,5, а далее, контролируя микрометром, снимаю очень малыми съемами до диаметра 16,00, периодически контролируя, пытаясь насадить на втулку сам патрон ER20. В принципе, мне удалось добиться плотной посадки на втулке.

 

Поставил индикатор, замерил биения внутреннего диаметра втулки — не более 0,01, даже после того, как снял ее со шпинделя и заново установил. Но вот китайский патрон ER20 дает уже биение 0,05, правда, на приличном вылете порядка 50 мм, что в принципе для целей фрезеровки большими диаметрами фрез или для зажатия отрезных дисков вполне приемлемо. Я в принципе не ожидал от китайских патронов за 300 рублей чего-то большего. Однако держится все жестко и функции свои выполнять будет. Итоговый результат на фото:



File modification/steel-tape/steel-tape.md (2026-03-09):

в процессе работы на станке происходит значительная выработка в местах трения каретки в ластохвосте. Пара трения там алюминий по алюминию (1.05-1.35 сухой, чем меньше - тем лучше), к сравнению алюминия по стали - 0.61, сталь по латуни 0.35, алюминия по латуни 0.17. Да еще и поверхность каретки у нас шершавая, то есть реальный коэффициент окажется еще больше чем справочный. Итого имеем плохую пару трения, и ее надо менять, это облегчит ход каретки и уменьшит износ направляющих. Я выбрал на сталь по латуни со стороны клина (так как у меня клин из латуни), ну и алюминий по стали для остальных мест каретки (так как собирают оклеивать только одну часть (неподвижную). И так процесс оклейки состоит из этапов: 1. подготовка поверхностей 2. Нарезание стальной ленты 3. Наклейка с помощью двухстороннего тонкого скотча 4. Финишные работы. И так в подготовку входит обезжиривание всех поверхностей как ластохвоста, так и стальной ленты (на самом деле лента из нержавейки). Обезжиривание делал с помощью ватных дисков и ватных палочек пропитанных в изопропиловом спирте. Обезжиривание делается непосредственно перед нанесением скотча на поверхность. Работать лучше в перчатках, так как прикасаться к поверхностям после обезжиривания нельзя. Так же можно подготовить поверхность стальной ленты немного зашкурив одну сторону - ту на которую будем наносить скотч, это придаст повышенную адгезию.
Этап 2: нарезка ленты, самый сложный я считаю, чем тоньше лента тем проще ее нарезать. У меня нержавеющая лента толщиной 0.1мм, очень жесткая, в этом есть как плюс - она не будет прогинаться после наклейки в процессе работы, так и минус - с ней сложнее работать при наклейке. Были опробованы 2 метода нарезания ленты - ножницами и отрезание строительным ножом по линейке. Ножницами - плохой вариант, как не старайся, будут загибы на краях - на фото видно. Хороший вариант - кусок деревяшки (желательно плотной древесины) с вставленным болтом и зажатой стальной линейкой с одной стороны. Между линейкой и деревяшкой заводим заранее отрезанный кусок ленты, с отметками (я прикладывал внутрь ластохвоста и чертилкой делал две линии в начале и конце). Далее прижимая линейку строительным ножом делаем 3 прохода с небольшим давлением, задача что бы нож набил себе путь. Дальше давление на нож увеличиваем и делаем еще 3 прохода, и повторяем процедуру пока не отрежем полосу. Проходов за 10 отрезается
этап 3: оклейку надо начинать с обезжиривания. Скотч надо наносить сперва на ластохвост. Пробовал наносить на ленту, этот вариант хуже - образуются заломы и пузыри на скотче - это негативно скажется в дальнейшем. Если наносить на ластохвост - скотч наносится отлично, отрезается ножом, но сложнее загнать отрезанную заранее в размер стальную полосу. Разглаживание начинаем от середины к краям. Далее я воспользовался разобранной кареткой и прогладил еще ей.  Полосу перед оклейкой так же обезжириваем. Далее надо завести край полосы внутрь ластохвоста, упирая ее в дальний край и прижимая там где нет скотча, позиционируем по торцам, смотрим что бы нижний край был максимально утоплен внутрь ластохвоста, и после этого начиная с середины и низа начинаем оклейку, пальцами не давая полосе прилипнуть сразу, она должна прилипать снизу вверх и из центра в стороны. Далее я прогладил оклееную сторону тыльной стороны ножа, далее опять кареткой, без нажима
Этап 4 состоит в том что бы срезать фаску или выступающие стороны. Торцы я рекомендую не отрезать, а загнуть, они прижмутся торцевыми накладками, не будут мешать, и даже будут помогать удерживать ленту от смещения. Фаску снимал фаскоснимателем, на фото, прижав сам блок к столу, и без надавливания фаскосниматель снимает тонкую стружку за несколько проходов можно добиться отличного результата, можно доработать надфилем локальные участки, например вначале где фаскосниматель не берет или зарывается. Ну и готовый результат на фото. Получилось достаточно качественно, после этой доработки ход стал мягкий, а болтанка прекратилась так как установил латунный клин (без оклейки лентой ластохвоста латунный клин быстро сработал бы алюминиевый ластохвост, поэтому оклейка стальной лентой обязательна)












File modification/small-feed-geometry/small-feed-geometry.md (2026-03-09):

Занялся поперечной подачей. План такой: сначала вывести плоскость стола поперечки, далее перевернуть и закрепить на продольной этим столом, так что плоскость соединительного ластохвоста окажется вверху, далее отфрезеровать ее с минимальным съемом, пришлифовать на шкурке. Для начала нанес маркер на стол поперечки и немного потер шкуркой закрепленой на плоскости. Видно что у нас две  полоски имеют вершины (краска стерлась там где шкурка брала). Сначала надфилем сточил их, дальше шлифовал на шкурке. Процесс муторный и грязный. Далее перевернул каретку и закрепил вверх ногами, так что бы можно было отфрезеровать плоскость соединительной детали. Очень хорошо выставил голову. И тут совершил одну ошибку: использовал цанги вместо патрона. Дело в том что цанги комплектные совершенно не подходят к этому станку, в шпинделе просто нет ответного конуса, поэтому цанга не может центрироваться. Я всегда использую токарный патрон для фрезеровки. Ну и замер что получилось. Было 0.5мм, стало 0.2мм, результат недостаточный.
Решил не бросать дело выведения геометрии продольной и поперечной подач, первый раз решил пошабрить, за одно и немного научиться, тем более на алюминии это не очень сложно. И так из инструмента скм шабер, шаберная краска и уголок УСП 120х120, его боковая шлифованая сторона, проверил по лекальной линейке, ровная для наших целей сойдет. Сначала нанес тонким слоем краску на УСП, достаточно буквально одной точки, и ватным диском промакивая распределяю равномерно по поверхности УСП. Важно понимать что нам не красить, нам сделать отпечаток, слой должен быть минимальный, почти прозрачный. Далее берем каретку и возюкаем ее по УСП с краской, получаес отпечаток - там где есть краска - поверхности соприкасались, именно их мы и будем срезать шабером. На фото видно что сначала брало только 2 гребня стола, а в конце уже на каждом гребне есть краска. Так я пошабрил плоскость столов поперечной и продольной подач. Ну и тест с индикатором: было до шабрения 0.2мм отклонения, стало 0.08мм на весь ход подачи. На этом остановлюсь









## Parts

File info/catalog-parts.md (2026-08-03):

## Каталог частей станков The fist tool
- Z001 Длинная балка 510х50х50, металл, красные крышки
- Z001B Длинная балка 510х50х50, металл, черные крышки
- Z001M Длинная балка 510х50х50, металл, черные крышки
- Z002 Z002B Z002M Стандартная балка 280х50х50, металл
- Z003 Z003B Z003M укороченная балка с отверстиями для крепления колонны фрезера, металл
- Z004MTS Моторный блок, металлический, 60Вт (без защитной крышки, цинковое покрытие крышек). Стандартный блок от серии станков высокой мощности 60Вт.
- Z004MTE Моторный блок, металлический, 60Вт (без защитной крышки, хромированное покрытие крышек)
- Z004M Вращающаяся бабка с шпинделем, укороченная, без редуктора, без мотора (цинковое покрытие крышек)
- Z004ME Вращающаяся бабка с шпинделем, укороченная, без редуктора, без мотора (хромированное покрытие крышек)
- Z004MS Вращающаяся бабка с шпинделем, укороченная, без редуктора, без мотора
- Z004-1M Двойной шкив от редектора моторного блока, 23 зубца и 60 зубцов, металл
- Z006-1 Двигатель 12В, 2А, 24Вт
- Z006-1L Двигатель 12В, 5А, 60Вт
- Z006 Двигатель с пластиковым корпусом, красный, 12В, 2А, 24Вт
- Z006B Двигатель с пластиковым корпусом, черный, 12В, 2А, 24Вт
- Z00603 Вентилятор со шкивом на вал мотора 24Вт
- Z007 Задняя бабка, красный и черный пластик, от базовой версии
- Z007ME Задняя бабка, металл, с подвижным центром (хромированное покрытие крышек)
- Z007MS Задняя бабка, металл, с подвижным центром (цинковое покрытие крышек)
- Z008 Поперечная подача (короткая каретка), черный пластик, от базовой версии
- Z008M Поперечная подача (короткая каретка), металл, без покрытия
- Z008ME Поперечная подача (короткая каретка), металл, хромированное покрытие
- Z008M-1 Ручка подачи без маховика
- Z009 Короткая продольная подача от базовой версии, пластик, 60*50*50 мм
- Z009L Длинная продольная подача от базовой версии, пластик, 230*50*50 мм
- Z009M Продольная укороченная подача, металл, 100*50*50 мм
- Z010 Продольная подача (длинная каретка), пластик, от базовой версии
- Z010M Продольная подача (длинная каретка), металл, цинковое покрытие крышек
- Z010ME Продольная подача (длинная каретка), металл, хромированное покрытие крышек
- Z011 3х кулачковый токарный патрон, металл, цинк
- Z011A 4х кулачковый токарный патрон, металл, цинк
- Z012 Тиски, черный пластик, от базовой версии
- Z012M Z012-M Тиски, металл, цинковое покрытие
- Z012MP Z012-MP Тиски, металл, черное покрытие
- Z013 Короткий распорный клин в ласточкин хвост, черный пластик
- Z013M Короткий распорный клин в ласточкин хвост, металл
- Z013ML Длинный распорный клин в ласточкин хвост, металл
- Z014 Маятниковый механизм лобзика, красный пластик
- Z014MN Маятниковый механизм лобзика, металл
- Z015 Эксцентриковый механизм лобзика, металл
- Z016 Неподвижный центр
- Z017 Шлифовальная пластина, пластик
- Z017M Шлифовальная пластина, металл, цинковое покрытие
- Z017ME Шлифовальная пластина, металл, хромированное покрытие
- Z017MP Шлифовальная пластина, металл, черное покрытие
- Z019 Подвижный центр на резьбу М12х1, для задней бабки
- Z022T Блок питания
- Z022 Фиксатор делительного устройства, пластик
- Z022M Фиксатор делительного устройства, металл, цинковое покрытие
- Z022ME Фиксатор делительного устройства, металл, хромированное покрытие
- Z022MP Фиксатор делительного устройства, металл, черное покрытие
- Z023 Делительный диск
- Z023A Поворотный блок, металл, цинковое покрытие
- Z023AE Поворотный блок, металл, хромированное покрытие
- Z023AP Поворотный блок, металл, черное покрытие
- Z023A-1 Переходной болт для поворотного блока
- Z024 Шлифовальная шкурка для шлифовального диска
- Z025 Стол лобзика, черный пластик
- Z025M Стол лобзика, металл, цинковое покрытие
- Z025ME Стол лобзика, металл, хромированное покрытие
- Z025MP Стол сверлильного станка, металл, черное покрытие
- Z026 Z025M Z026MP Стол лобзика\фрезерного\сверлильно станка
- Z027 Ручка подачи сверлильного станка, черный пластик
- Z027M Ручка подачи сверлильного станка, металл, цинковое покрытие
- Z027MP Ручка подачи сверлильного станка, металл, черное покрытие
- Z028 Защита? красный пластик
- Z029 Часть лобзика, красный пластик
- Z030 Проставка высотой 25мм (50мм * 50мм * 25мм), красный пластик
- Z030M Проставка высотой 25мм (50мм * 50мм * 25мм), металл, цинковое покрытие
- Z030ME Проставка высотой 25мм (50мм * 50мм * 25мм), металл, хромированное покрытие
- Z030MP Проставка высотой 25мм (50мм * 50мм * 25мм), металл, черное покрытие
- Z030MA Проставка удлиненная высотой 50мм, размеры 75мм * 50мм * 50мм, металл, пластиковые черные крышки. Для моторного блока.
- Z030MAP Проставка удлиненная высотой 50мм, размеры 75мм * 50мм * 50мм, металл, хромированные крышки. Для моторного блока.
- Z030MB Проставка высотой 50мм "кубик" 50мм * 50мм * 50мм, металл, пластиковые черные крышки
- Z030MBP Проставка высотой 50мм "кубик" 50мм * 50мм * 50мм, металл, хромированные крышки
- Z030MR Проставка высотой 50мм "кубик" 50мм * 50мм * 50мм, металл, пластиковые красные крышки
- Z031 Z031T Ремень редуктора мторного блока для двигателя 60 Вт
- Z033 Подручники для резцов (упоры) для деревообрабатывающего станка, черный пластик, от базовой версии
- Z033M Z033ME Z033MLE Z033ML Z033MLB подручники для резцов (упоры) для деревообрабатывающего станка, металл
- Z034 Задняя крышка моторного блока, пластик, красный
- Z034B Задняя крышка моторного блока, пластик, черный
- Z034MP Задняя крышка моторного блока, металл, хромированное покрытие
- Z036 Конус для выставления центров
- Z038 Защита для токарного станка
- Z038P Уголок крепления резца на поперечной подаче?, металл. Не опознано
- Z042 Одиночные гайки фиксации в ласточкин хвост, черный пластик
- Z042A Одиночные гайки фиксации для Т-паза
- Z042M Одиночные гайки фиксации в ласточкин хвост, металл
- Z043 Двойные гайки фиксации в ласточкин хвост, черный пластик
- Z043M Двойные гайки фиксации в ласточкин хвост, металл
- Z044 Уголок крепления резца на поперечной подаче, пластик, от базовой версии
- Z044M Уголок крепления резца на поперечной подаче, металл, цинковое покрытие
- Z044ME Уголок крепления резца на поперечной подаче, металл, хромированное покрытие
- Z044MT Резцедержка короткая
- Z044MTL Резцедержка длинная (расчитана на работу со станками с увеличенным размером над станиной за счет проставки 25мм)
- Z045A Гайка цангового патрона
- Z060 Пилка лобзика (короткая)
- Z061 Не опознано
- Z061 Набор латунных цанг (1, 2, 2.5, 3, 3.5, 4, 5, 6 мм)
- Z061-08 Цанга латунная 6мм
- Z061B Z061C Z061C Расточные головки для фрезера, летающая фреза
- Z062 Набор абразивов и коррщетка
- Z062M Набор алмазного инструмента (коронка и маленькая конусная фреза)
- Z070B Отвертка под гайки м4
- Z071 Ключ (штревель) фиксации шпинделя, Г-образный 3мм ключ
- Z072 Стержень для затяжки патрона (или тисков)
- Z073 Z073B Шаблон для разметки центра заготовки
- Z077-1 Резец 4х4 HSS
- Z078 Длинная отвертка
- Z08001 Усиливающая пластина длинная 125 мм * 50 мм * 4 мм, металл
- Z08001-A Усиливающая пластина короткая, металл
- Z08003 Усиливающий уголок 50мм * 50мм * 50мм, металл, 

- B001 Дуга от лобзика
- D001 Адаптер М12х1 на конус В10, для сверлильного патрона
- B001-2 B001P-2 B001P-2P направляющая пилки лобзика, металл
- F001 Ключ для затяжки гайки цангового патрона
- F003 Пластиковое основание крепления станка
- UZ01401M сердцевина маятникового механизма лобзика

## Изображения некоторых деталей из каталога
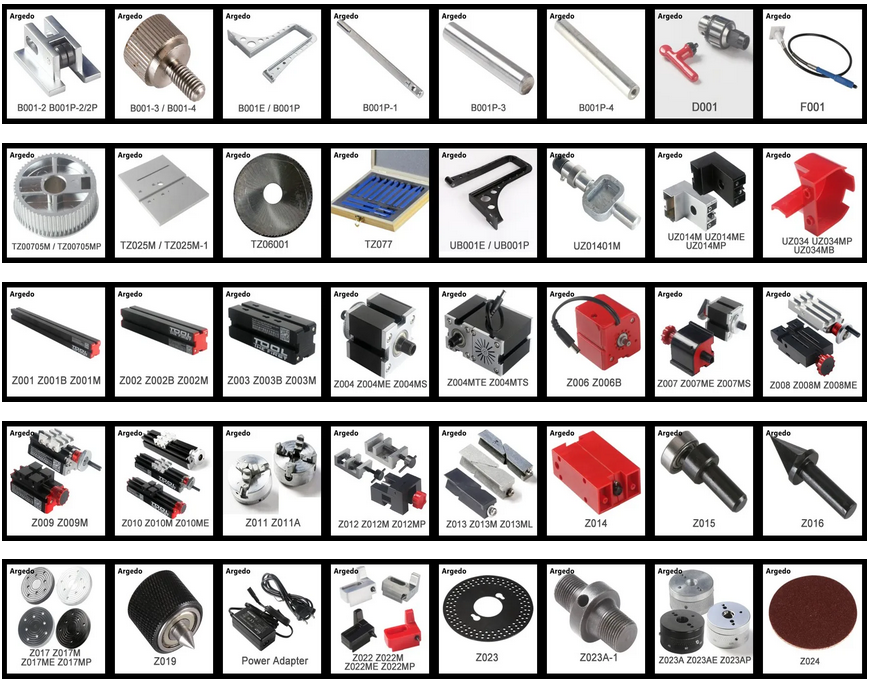
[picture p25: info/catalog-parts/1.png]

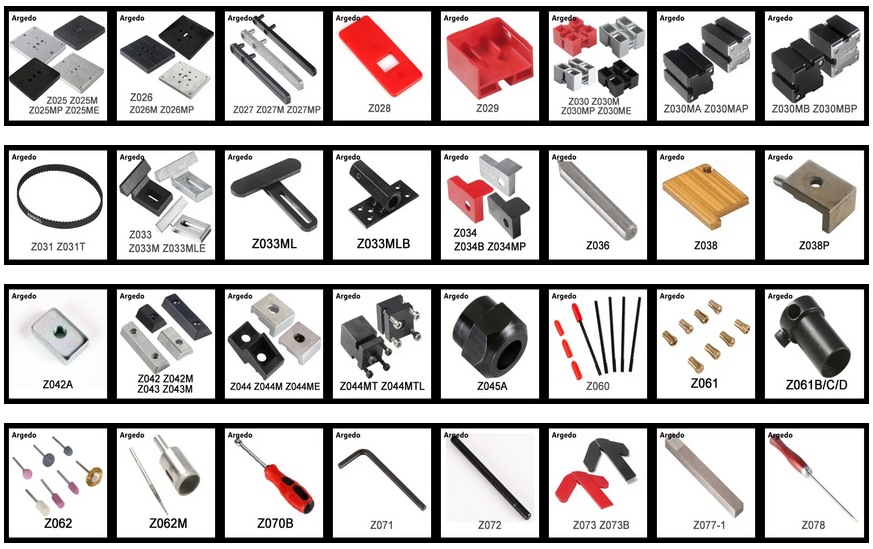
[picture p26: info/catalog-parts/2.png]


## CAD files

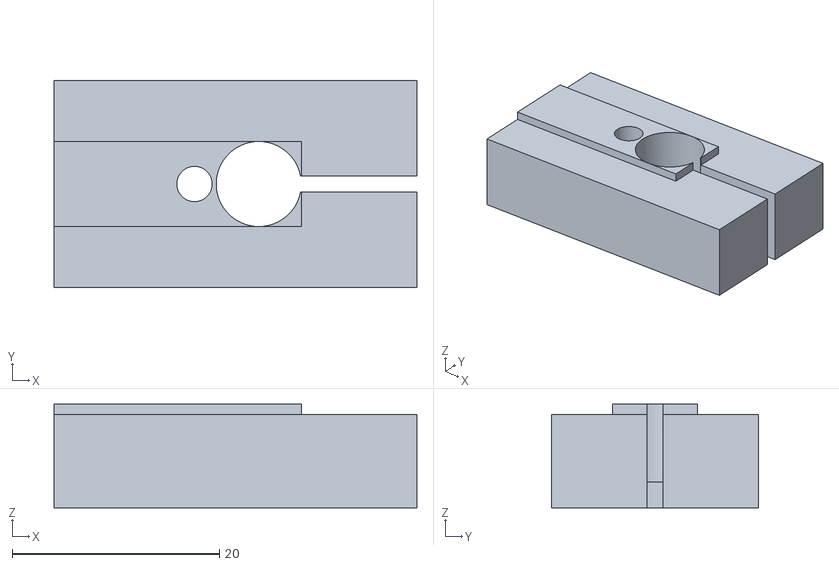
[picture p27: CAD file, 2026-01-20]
3d/conductor-nuts-t5/conductor-nuts-t5.stl
35.0 x 20.0 x 10.0

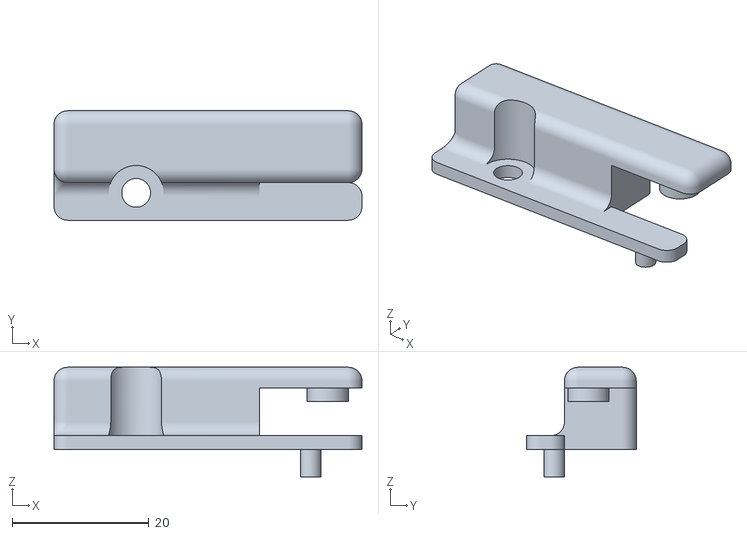
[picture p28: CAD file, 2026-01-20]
3d/drilling-machine-lever-holder/drilling-machine-lever-holder.stl
45.0 x 16.0 x 16.0

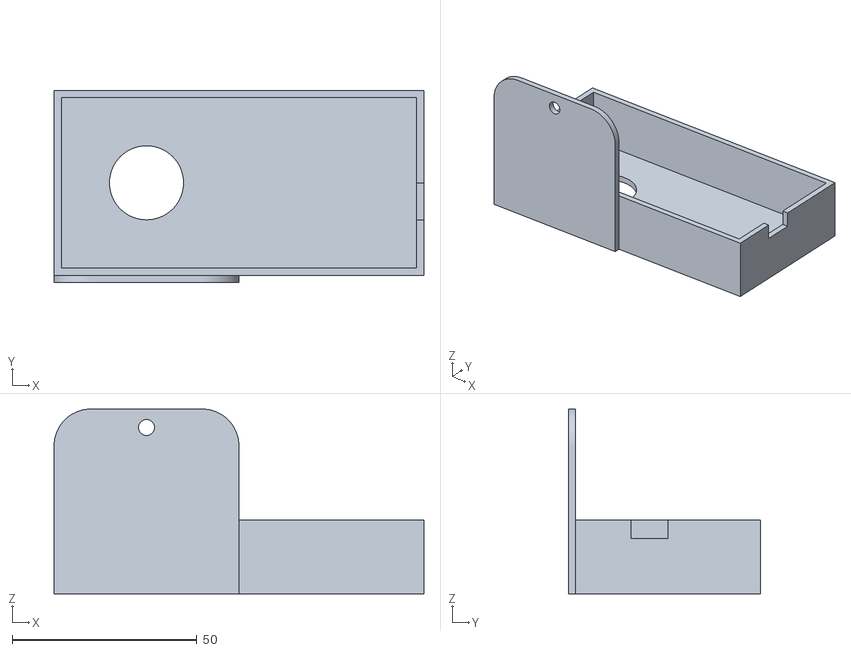
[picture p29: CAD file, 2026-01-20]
3d/engine-block-cover/engine-block-cover.stl
100.0 x 52.0 x 50.0

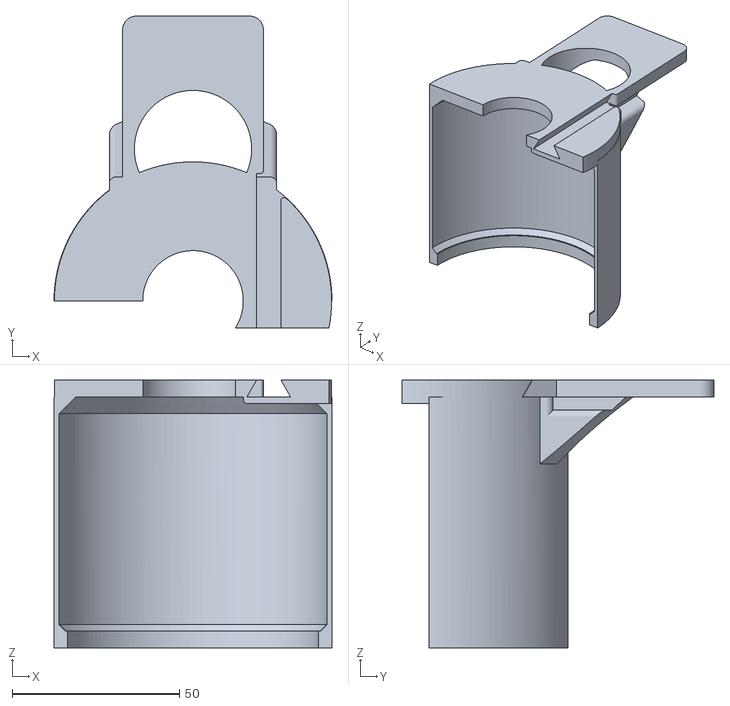
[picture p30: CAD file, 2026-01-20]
3d/motor-protection-horizontal-milling/motor-protection-horizontal-milling-1.stl
83.0 x 93.0 x 80.0

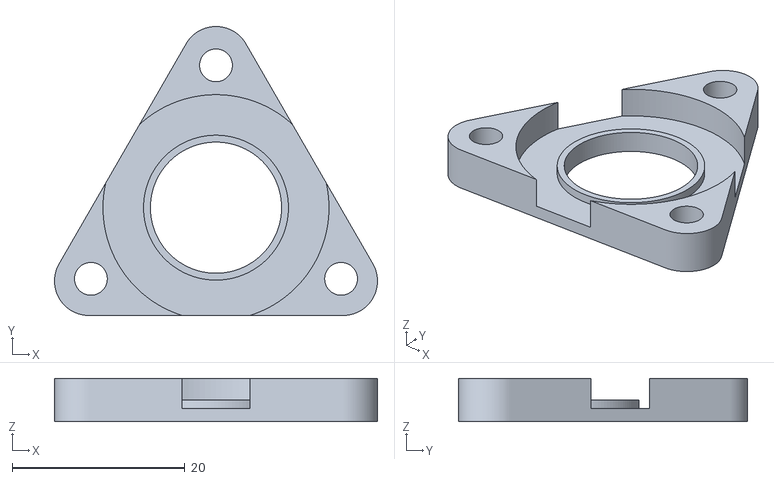
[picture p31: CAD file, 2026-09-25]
3d/Проточка-подшипников-1.stl
37.4 x 33.5 x 5.00

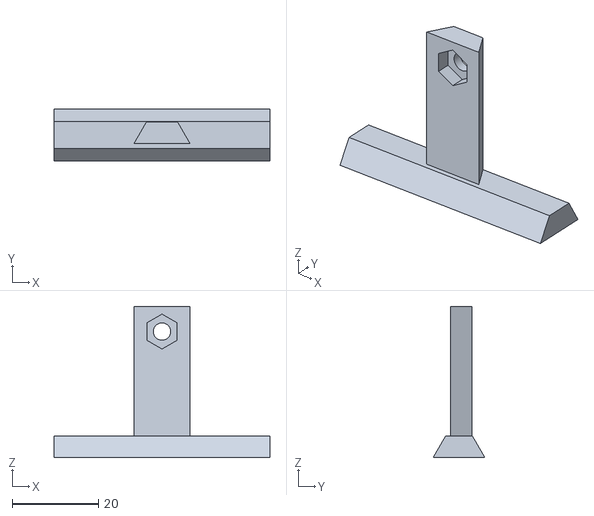
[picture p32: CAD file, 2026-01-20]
3d/motor-protection-horizontal-milling/motor-protection-horizontal-milling-2.stl
50.0 x 12.0 x 35.0

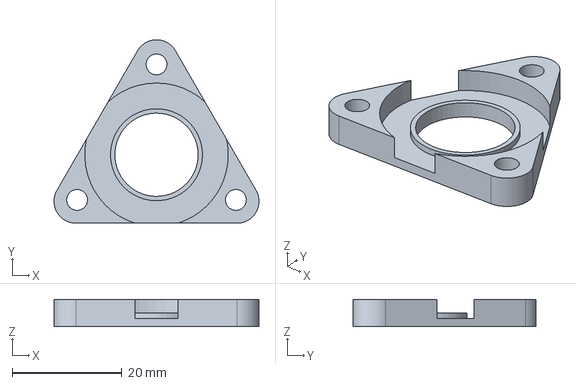
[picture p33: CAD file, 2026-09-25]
3d/Проточка-подшипников.FCStd
37.4 x 33.5 x 5.00 mm

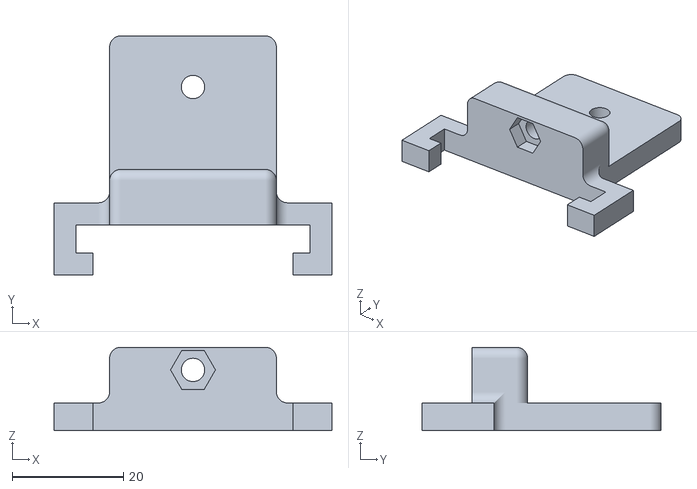
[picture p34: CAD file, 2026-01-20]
3d/motor-protection-horizontal-milling/motor-protection-horizontal-milling-3.stl
50.0 x 43.0 x 15.0

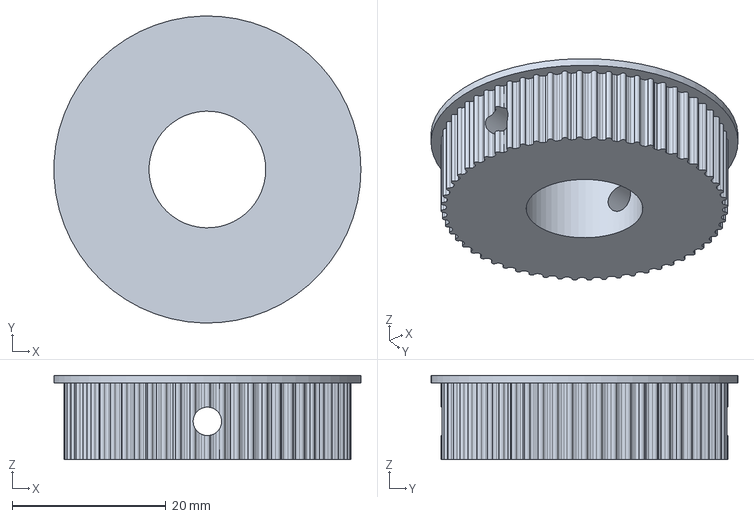
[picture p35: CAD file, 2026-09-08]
3d/Шестерня-шпинделя.FCStd
40.0 x 40.0 x 11.0 mm

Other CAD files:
3d/Шестерня-шпинделя.stl

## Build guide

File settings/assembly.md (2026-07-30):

## Варианты сборки разных станков

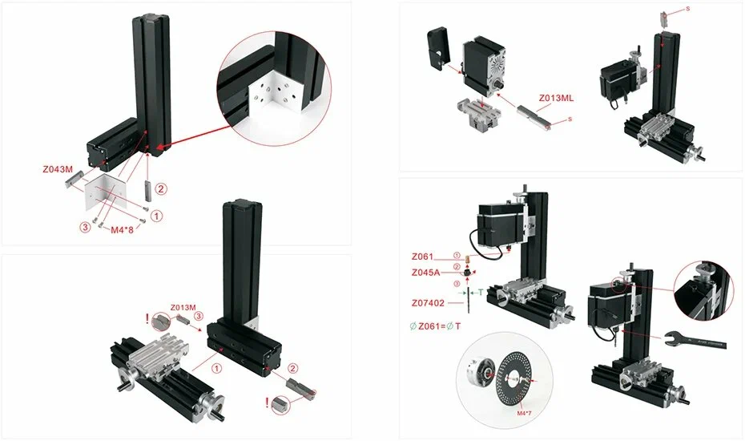
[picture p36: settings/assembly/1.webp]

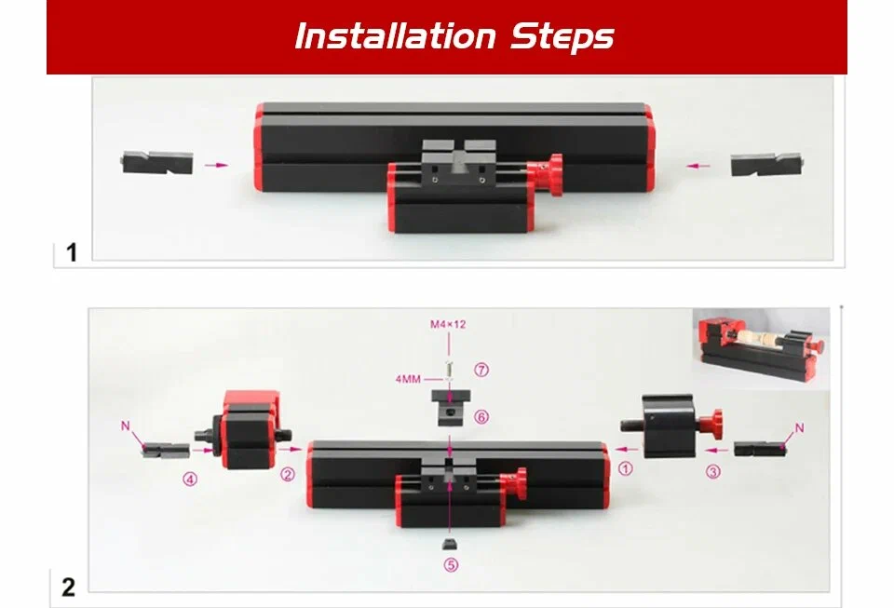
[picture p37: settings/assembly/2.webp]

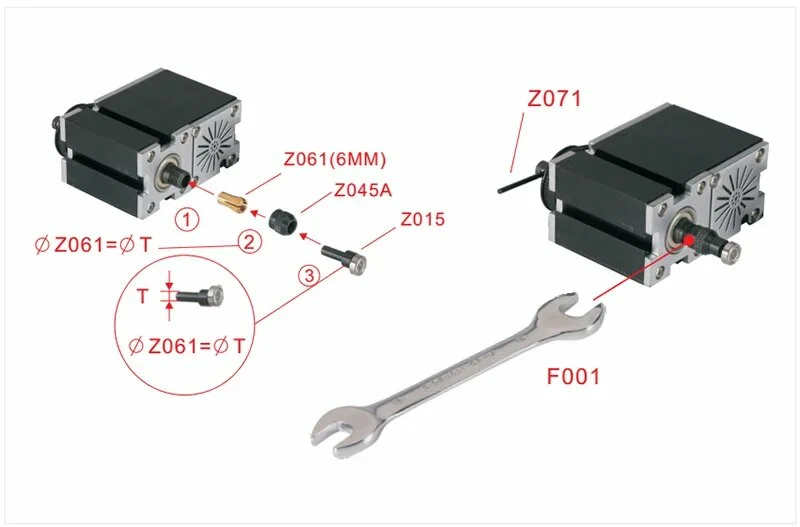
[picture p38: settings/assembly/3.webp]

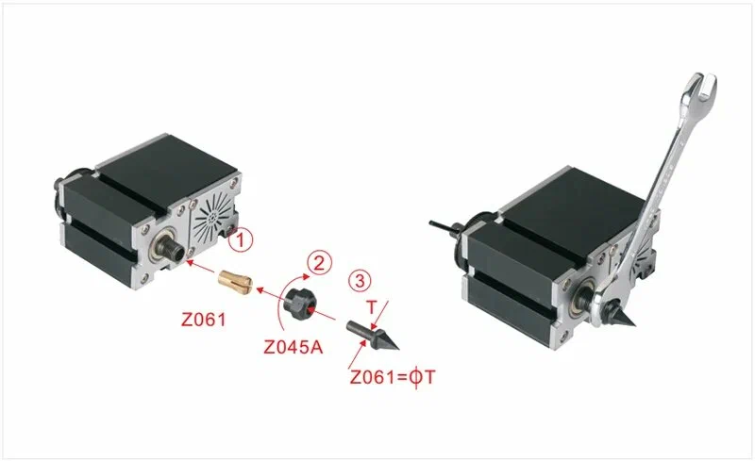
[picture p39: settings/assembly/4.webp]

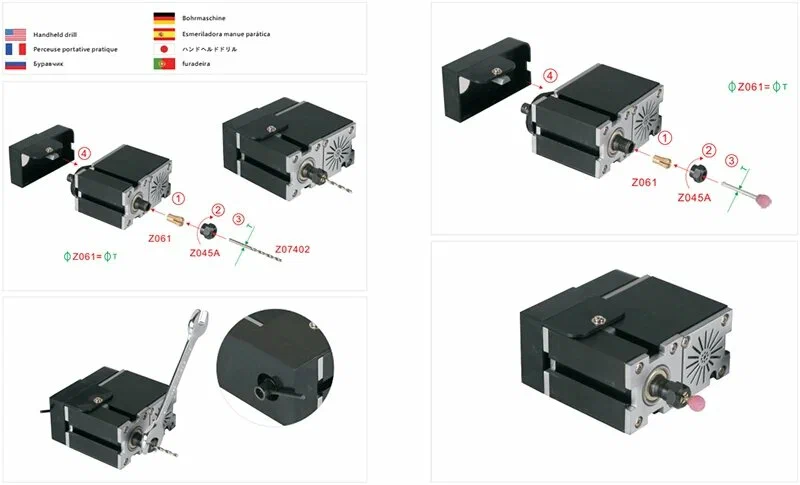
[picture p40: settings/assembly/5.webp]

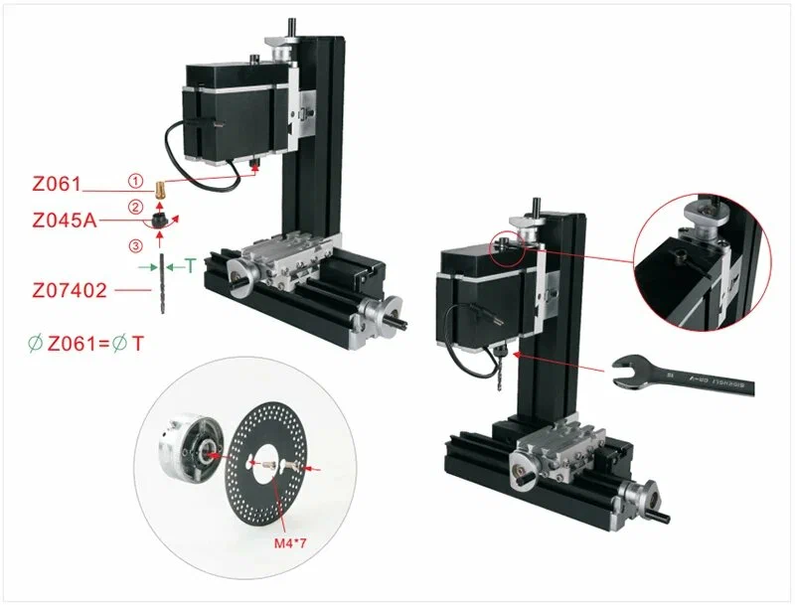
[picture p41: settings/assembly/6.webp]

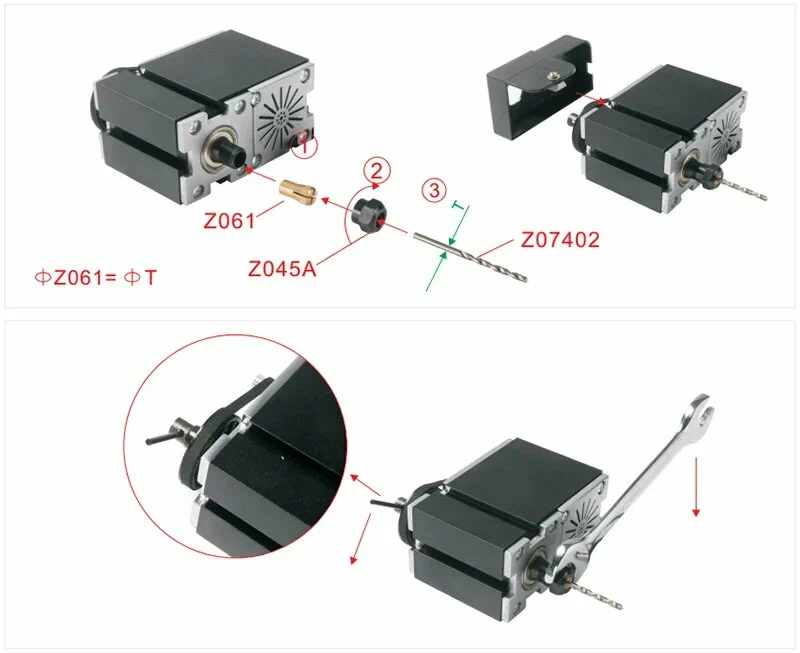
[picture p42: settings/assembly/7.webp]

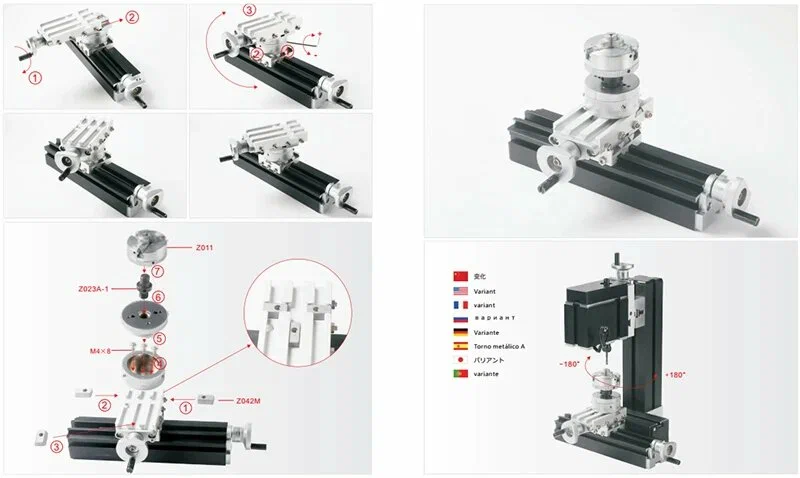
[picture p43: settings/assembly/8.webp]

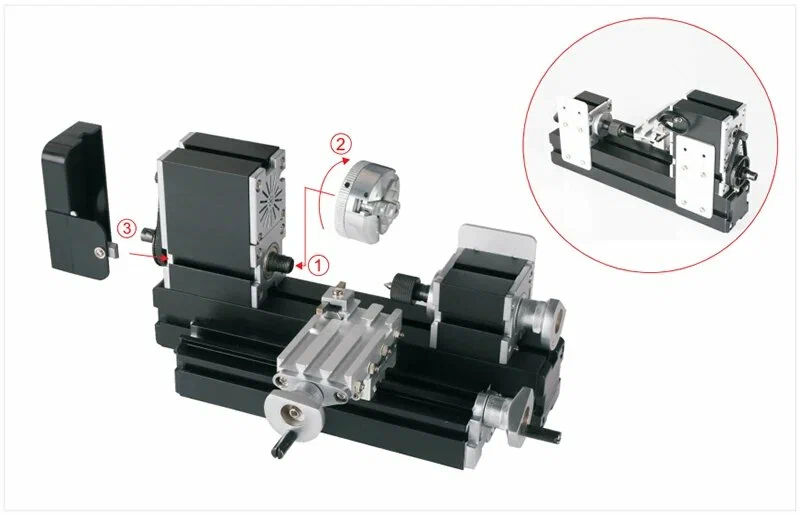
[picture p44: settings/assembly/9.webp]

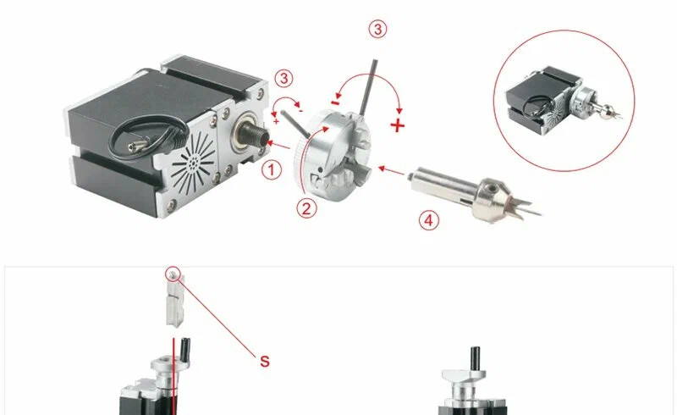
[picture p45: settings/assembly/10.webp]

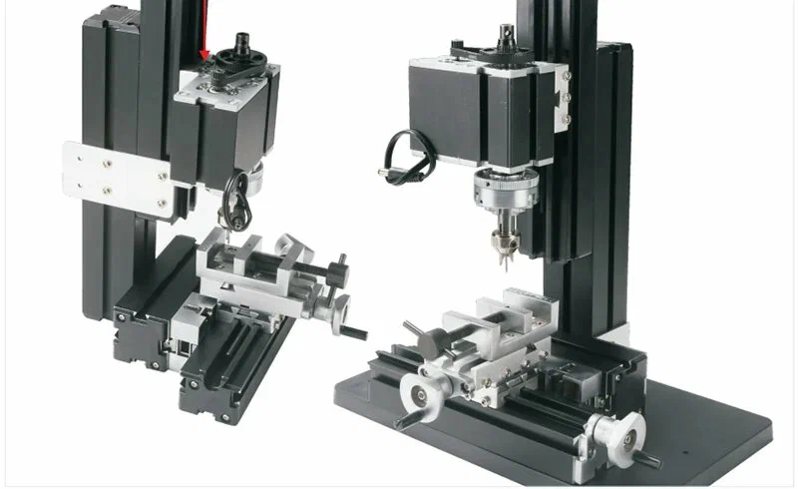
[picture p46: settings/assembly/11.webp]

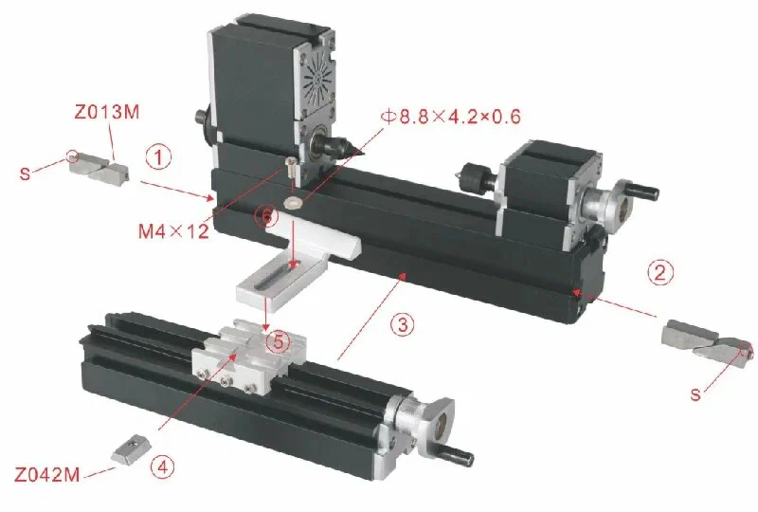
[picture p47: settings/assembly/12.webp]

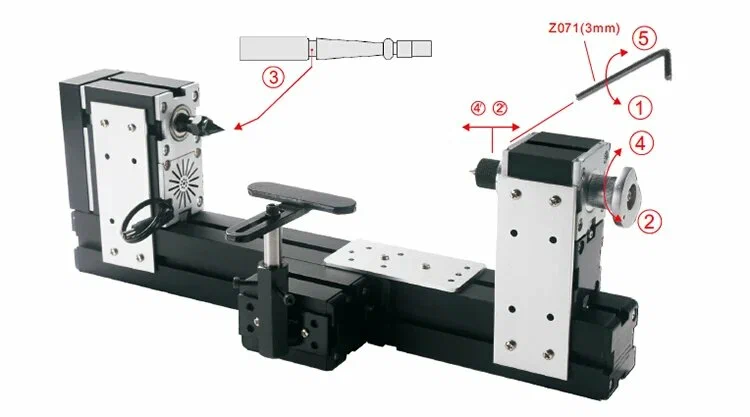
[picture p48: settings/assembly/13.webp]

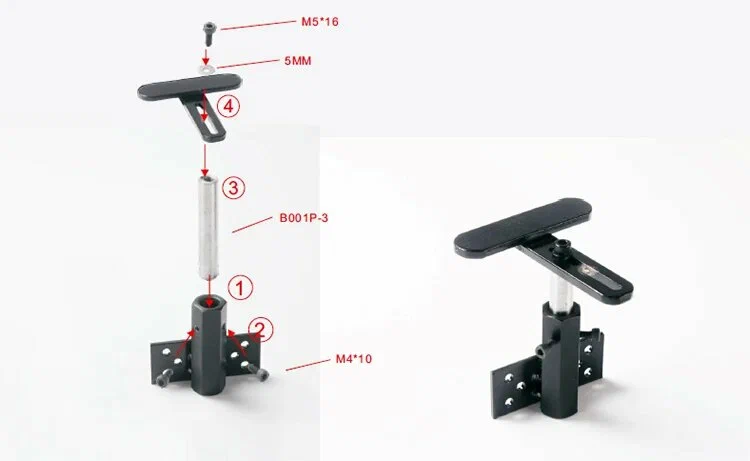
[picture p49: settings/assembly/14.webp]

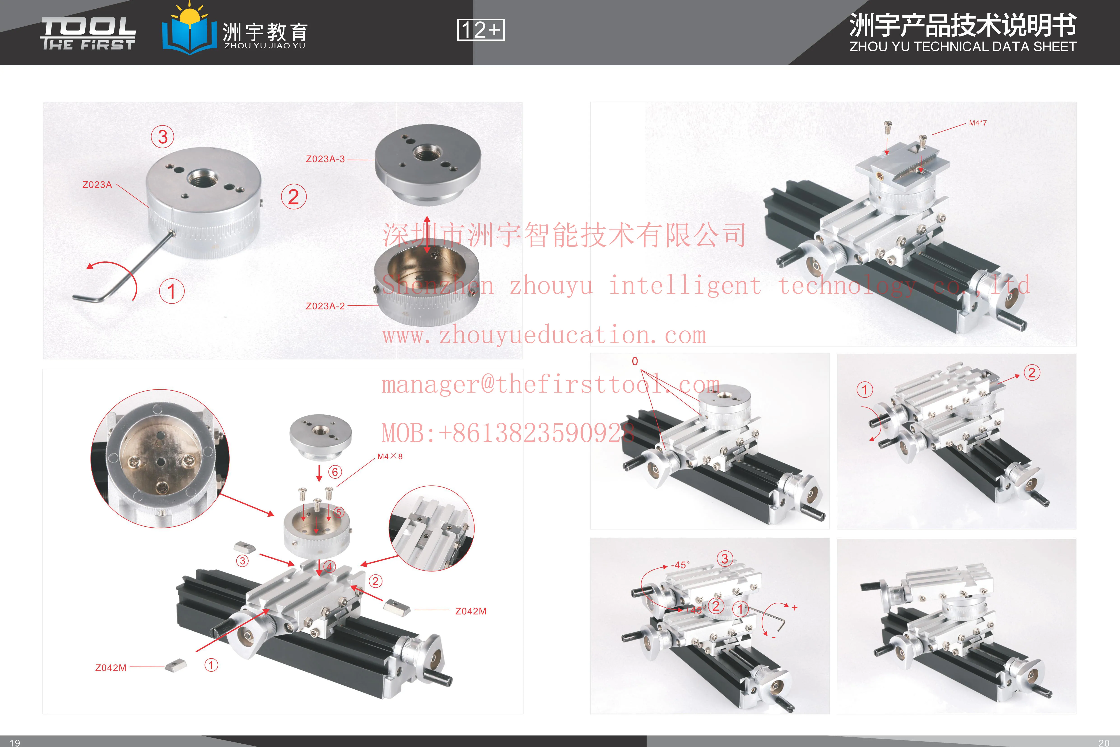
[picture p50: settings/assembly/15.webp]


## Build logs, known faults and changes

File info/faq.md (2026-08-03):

# Ответы на часто задаваемые вопросы

Я собрал популярные вопросы с маркетплейсов где продают станки и решил на них ответить. Ответы будут исходя из моего опыта работы со станком The first tool (металлическая версия 60 ватт), черная рама, черные или металлические заглушки). 
Большинство ответов применимо к станкам Xendoll и Unimat (так же металлических версий). Это мой личный опыт эксплуатации станка, измерение геометрии и жесткости и серьезной его переработки, так же общения с другими владельцами таких станков в нашем телеграмм канале

Какой материал может обрабатывать станок?
- Дерево, пластики, цветной металл (алюминий, дюраль, латунь, бронзу) в заводском своем виде. Сталь - условно, с небольшими съемами. С учетом серьезной доработки станка - даже серьезные типы сталей до нержавейки.

Какого размера можно обрабатывать детали?
- Для токарного станка это заготовки до 45мм диаметром на зажатии обратными кулачками на штатном патроне. Для таких диаметров скорость вращения шпинделя порядка 3000об\мин великовата, ее нужно снижать хотя бы до 1000 об\мин. Длина заготовки 110мм максимум
- Для фрезерного станка 150 мм (по продольной подаче) х 50 мм (по зажатию штатных тисков, но ход поперечной подачи 32мм) х 100мм (условно, по максимальному подъему вертикальной подачи).
- Однако я обрабатывал детали и по 300мм, разумеется с перестановкой. Существует длинная балка 500мм, которая существенно расширяет габариты обрабатываемых деталей

Какое расстояние над станиной для токарного станка?
- до 75мм при использовании проставки 50мм (или закреплении блока вверх ногами). При закреплении без проставки 25мм - не имеет значения, кулачки патрона упираются в балку и так точить не получится. При закреплении комплектной проставкой 25мм - высота над станиной 50мм.

Можно ли точить шестерни на станке?
- да, существует комплект для точения шестерен из мягких материалов, это поворотная бабка + фиксатор + делительный диск. Конечно правильной формы зубов получить не удастся, но требуемое количество треугольных зубов получить можно. Конечно можно изготовить только самые простые прямозубые шестерни

Можно ли обрабатывать АМГ3 или АМГ6? 
- да, это алюминиевые сплавы, отлично обрабатываются на станке даже без доработок. Для фрезерования советую использовать изопропиловый спирт в виде СОЖ в малых количествах подкапывая на деталь, так стружка будет лучше сходить с инструмента, будет меньше вибраций и станку проще работать.

Можно ли применять фрезы больше чем 6мм?
- да, можно зажать фрезу в токарный патрон. Фрезеровать нужно очень осторожно если речь о заводском варианте станка. При модификации после усиления жесткости - фрезеровать дюраль типа Д16Т фрезами ф8 и ф10 можно вполне спокойно. Если говорить о дереве и пластиках то фрезы крупнее штатной ф6 вполне будут работать на станке без доработок.

Можно ли переделывать станок (из токарного собрать фрезерный или из фрезерного собрать токарный)?
- да, станок модульный, можно покупать дополнительные детали (например токарный патрон или тиски и цанги) и собирать свои варианты станков на любой вкус. Все части станков The first tool совместимы друг с другом, но не совместимы с Xendoll. Если у вас "синий" станок марки Xendoll тогда надо покупать части именно этого производителя.

 Чем отличаются станки горизонтальный фрезерный (TZ20005MM) и вертикальный фрезерный (TZ20005M)?
 - ничем, это просто два варианта сборки одних и тех же деталей, выбирайте просто который дешевле (зачастую дешевле горизонтальный фрезерный). Из горизонтального фрезерного вертикальный фрезерный собирается за пару минут.

Что выбрать фрезерный или токарный вариант для покупки?
- зависит от ваших потребностей, но если вы выбираете с расчетом что хотите и фрезерный и токарный - в фрезерном обычно комплектация солиднее. так же можно посмотреть вариант покупки отдельно балок, крепежа, моторного блока и тд, возможно это выйдет дешевле чем покупать сразу комплект.

Можно ли приобрести отдельно цанги?
- да, они продаются как комплектом цанг из 6шт, так и можно купить отдельно одну цангу 6мм. Обычно в фрезерном варианте идет 1 цанга 6мм и набор нужно покупать отдельно. Для станка Xendoll идет сразу набор цанг.

Возьмет ли сталь?
- без серьезной доработки - скорее нет чем да. Грызть понемногу он будет, но это будет больно и сложно. Первое что нужно это снижение оборотов - 3000об\мин для стали это очень много. На блоке который идет со станком регулировки оборотов нет, но можно купить блоки питания с регулировкой отдельно. Выбирайте блоки с параметрами минимум 12V 5А. Если вам нужно постоянно обрабатывать стальные заготовки - лучше купить другой станок, этот все таки не предназначен для постоянной обработки стали.

Какой двигатель установлен?
- RS550 (60watt)

Можно ли поставить стальной патрон, например SANOU K01-50 или K01-65?
- на стандартный шпиндель нет, резьба на стандартном шпинделе м12х1, на патроне K01-50 резьба 14х1. Однако можно купить шпиндель который подойдет для такого патрона. Так же есть варианты с изготовлением переходника м12х1 на м14х1

Этот станок работает от розетки?
- да, блок питания работает от розетки 220v, однако сам станок работает от постоянного напряжения 12V, оно полностью безопасно

Где приобрести и какие резцы приобрести?
- в интернете на маркетплейсах, есть несколько вариантов: со сменными пластинками - они дороже, но их не нужно затачивать, просто замена пластинки когда затупилась. Пластинки продаются отдельно пачками и поштучно. Второй вариант резцы с напайками или цельные из быстрореза (HSS, Р6М5) - они дешевле, но их нужно учиться затачивать. Главное на что нужно обратить внимание это габарит державки, вам подойдут державки 8х8мм или 4х4мм для стандартной резцедержки которая идет со станком. Можно заменить резцедержку от более взрослого станка типа W210, тогда будут подходить державки до 12х12мм.

Какие фрезы купить?
- выбирайте исходя из потребностей, обычно самая ходовая фреза 6мм (четырехзубая) из быстрореза или твердосплавная. Не покупайте дорогие фрезы, они для других станков, вы не сможете раскрыть потенциал таких фрез. Для этого станка подойдут самые дешевые фрезы по металлу, обычно они в районе от 200 до 500р за штуку.

Какие подшипники установлены в шпинделе?
- типоразмера 6000ZZ (10х26х8 мм, однорядный с со стальными защитными крышками с двух сторон)

Можно ли нарезать резьбу на станке?
- разве что плашкой\метчиком. В данном станке нет автоподачи на продольной каретке требуемой для нарезания резьб, нарезать резьбы резцом в заводском варианте не получится.

Можно ли резать конусы, регулировка угла есть?
- да, существует поворотный блок (артикул Z023A, Z023AE) с помощью которого можно поставить две каретки друг на друга и поворачивать их по оси. Нужно учесть что центр уйдет сильно вверх поэтому требуется использовать проставочные блоки 50мм под переднюю и заднюю бабки.

Есть ли регулировка оборотов?
- нет, в поставляемом блоке питания нет регулировки напряжения, но можно докупить любой регулируемый блок питания с параметрами 0-12V 5А или более. Я использую лабораторный источник питания типа 3010.

Блестящие накладки на торцах балок это пластик или металл?
- это хромированный металл

Идет ли нижняя платформа к которой крепится станок в комплекте?
- да, для the first tool это пустотелая пластиковая панель. Для Xendoll - из дерева (мдф). Пластиковая в целом непригодна к использованию

Чем смазывать станок?
- любым жидким маслом машинным или универсальным типа И-20, для швейных машин, трансмиссионным и тд. Я смазываю трансмиссионным маслом

Из какого материала сделан штатный патрон?
- из цинкового сплава (серые патроны). Существуют из алюминия - они лучше, но покупать нужно отдельно, опознаются по характерным отверстиям на лицевой стороне губок патрона

Из какого материала сделаны остальные части станка (каретки, балки)?
- из сплава алюминия, предположительно АМГ3. Они тверже чистого алюминия примерно в 2 раза.

Как закреплен патрон?
- конус 1:15 с резьбой м12х1

Какая точность станка?
- зависит от умения точить) для станка the first tool заявленная точность на лимбах подачи 0.04мм\деление, для станков Xendoll будет в 2 раза хуже (там шаг винтов подач 2 мм\оборот). В эксплуатации при должной сноровке мне удается ловить пару соток.

Можно ли купить отдельно приводной ремень для моторного блока?
- да, они продаются отдельно

Станок игрушка или на что то способен?
- этот станок для обучению токарному или фрезерному делу. Он подойдет для хобби (всякие пушечки для кораблей или колеса модельных самолетов или втулочки, оси, штуцеры из металла точить, помогать в домашнем ремонте) - с этим он справится. Станок простой, легкий, компактный - нужно достал из шкафа, не нужно убрал, ему не требуется отдельно выделенного места. Если вы хотите использовать его на постоянную работу для зарабатывания денег или для обработки стали - это не ваш станок. Поэтому прямо отвечая на вопрос - нет не игрушка в умелых руках, хотя и детей обучать на нем вполне можно (под присмотром взрослых разумеется и после объяснения элементарных требований безопасности и обеспечения как минимум защитными очками\маской).

Станок кривой косой, все болтается, сплошные люфты, как на нем можно что то сделать?
- в завода станок поставляется собранным "до кучи" что бы ничего не потерялось. Никак не настроен. Требуется полная его разборка, изучение конструкции и сборка с протягиванием и настройкой прижима клиньев подач, степени затяжки гайки на лимбах и тд.

Можно ли купить дополнительные детали от станка? Например каретку, еще одну балку, тиски, токарный патрон и тд
- да, они продаются на маркетплейсах. Обычно что бы найти то что вам нужно нужно искать по артикулу детали, перечень всех частей станка продающихся отдельно с их артикулами по [ссылке](catalog-parts.md)

Где можно пообщаться с владельцами станков и задать вопросы или обменяться опытом?
- у нас есть [телеграмм канал Мини-станки](https://t.me/TheFirstToolRussia)

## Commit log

2026-01-20 Rename Крышка моторного блока левая.stl to engine-block-cover
2026-01-20 Rename engine-block-cover to engine-block-cover.stl
    [engine-block-cover.stl]
2026-01-20 Rename engine-block-cover.stl to engine-block-cover.stl
    [engine-block-cover.stl]
2026-01-20 Rename Защита горизонтального фрезера.stl to motor-protection-horizontal-milling.stl фрезера.stl
    [motor-protection-horizontal-milling.stl фрезера.stl]
2026-01-20 Rename motor-protection-horizontal-milling.stl фрезера.stl to motor-protection-horizontal-milling-1.stl
    [motor-protection-horizontal-milling-1.stl]
2026-01-20 Rename Защита горизонтального фрезера-крепление1.stl to motor-protection-horizontal-milling-2.stl
    [motor-protection-horizontal-milling-2.stl]
2026-01-20 Rename Защита горизонтального фрезера-крепление2.stl to motor-protection-horizontal-milling-3.stl
    [motor-protection-horizontal-milling-3.stl]
2026-01-20 Rename Держатель рычага сверлилки.stl to drilling-machine-lever-holder.stl
    [drilling-machine-lever-holder.stl]
2026-01-20 Rename Кондуктор для фрезеровки гаек Т5.stl to conductor-nuts-t5.stl
    [conductor-nuts-t5.stl]
